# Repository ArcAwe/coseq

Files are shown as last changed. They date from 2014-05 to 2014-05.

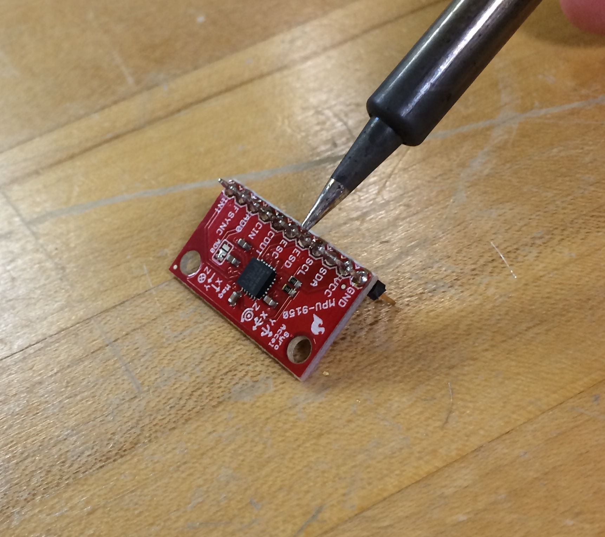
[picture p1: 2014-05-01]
photos/IMG_0470.jpg

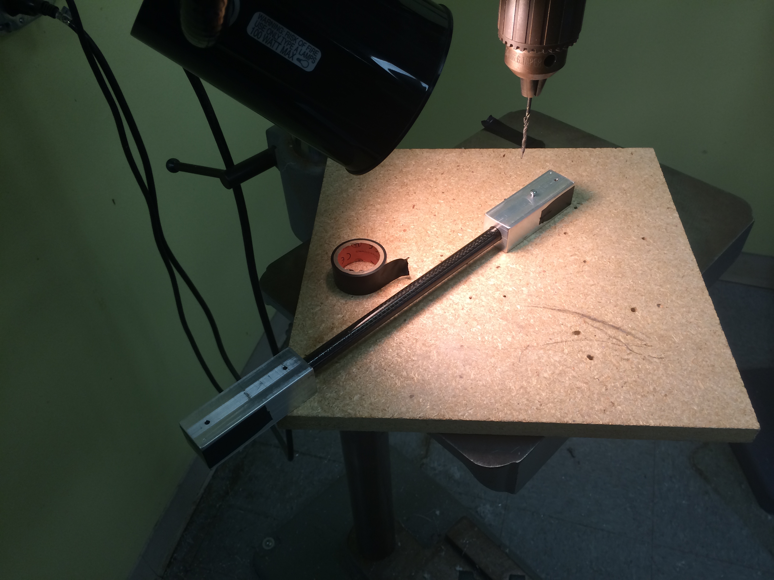
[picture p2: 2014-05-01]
photos/IMG_0632.JPG

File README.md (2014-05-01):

<i>coseq</i>
============

Cadet Open Source Extensible Quadcopter (COSEQ) Design Documents and Code.

Written and compiled by G. Holland Gibson - 2014
Originally as part of his Honors Project @ The United States Military Academy. 

Open Source
===========

This is a primarily open-source design (and work in progress) to accomplish 3 extensible and adaptable components that operate 
independently of each other in order to provide a stable airborne platform in a quadcopter form.

Written under the MIT license except where otherwise noted (using other peoples' open source code). See LICENSE for more info.

1] Hardware:
-----------
The Hardware is a very stable, and strong, yet lightweight construction

2] Controller: 
-------------
The controller uses Python running on a raspberry pi (battery powered) with a USB controller/gamepad.

3] Embedded Electronics: 
-----------------------
Parallax Propeller as host system.

Open Source / Freeware used:
============================
Google SketchUp
    http://www.sketchup.com/<br>
SimpleIDE
    http://learn.parallax.com/propeller-c-set-simpleide<br>
TextWrangler
    http://www.barebones.com/products/textwrangler/<br>
netfabb Basic
    http://www.netfabb.com/basic.php<br>

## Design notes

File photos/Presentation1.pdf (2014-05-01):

# Cadet Open Source Extensible Quadcopter

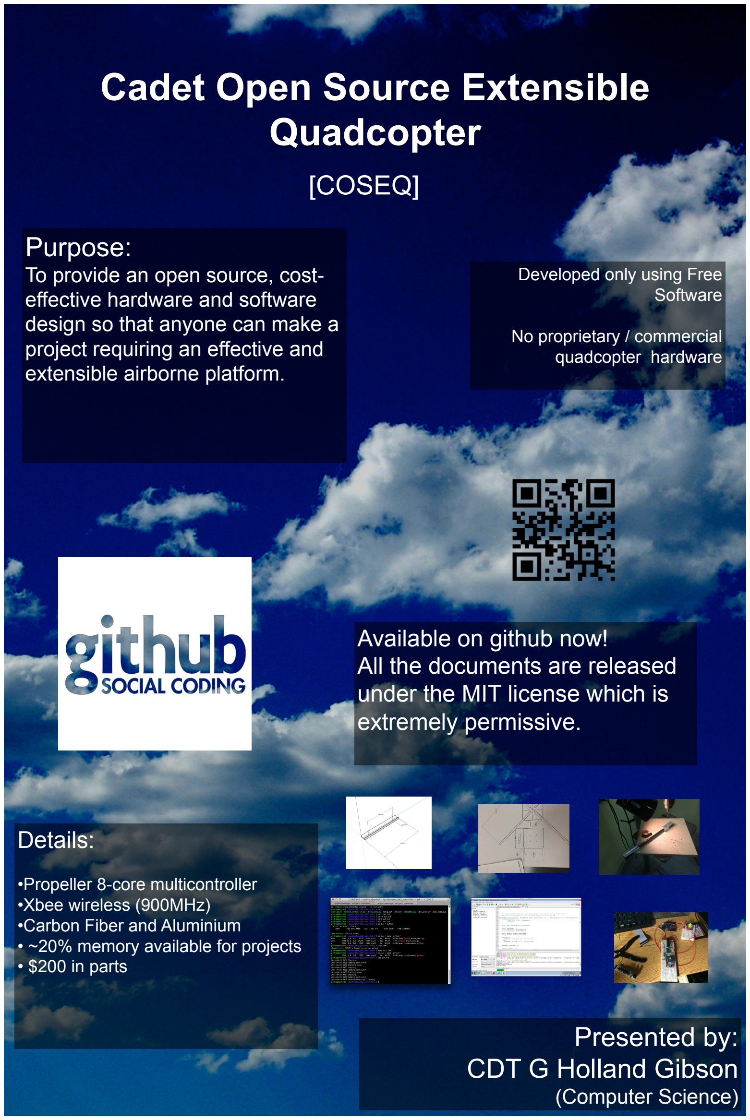
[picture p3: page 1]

## [COSEQ]

## Presented by: CDT G Holland Gibson

(Computer Science)

## Purpose:

To provide an open source, costeffective hardware and software design so that anyone can make a project requiring an effective and extensible airborne platform.

## Available on github now! All the documents are released under the MIT license which is

extremely permissive.

Developed only using Free
Software

No proprietary / commercial quadcopter hardware

## Details:

•Propeller 8-core multicontroller •Xbee wireless (900MHz)
•Carbon Fiber and Aluminium
- ~20% memory available for projects
- $200 in parts

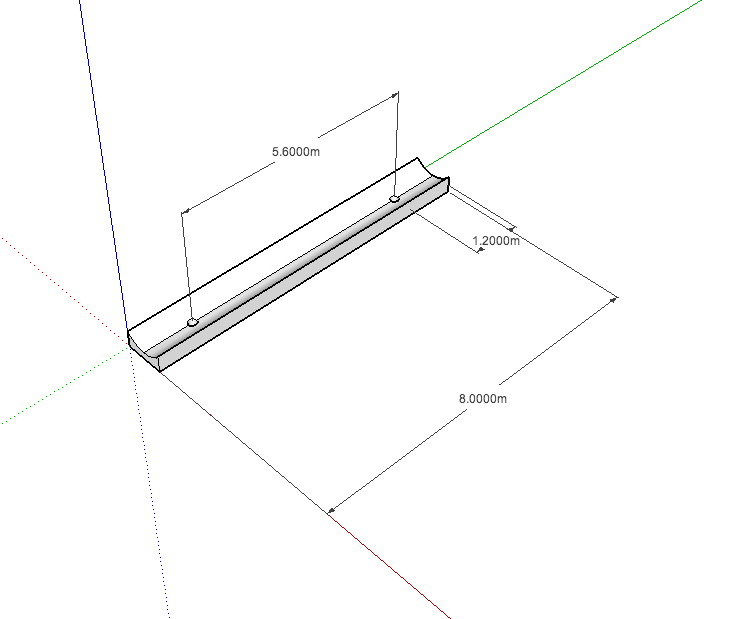
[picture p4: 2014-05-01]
photos/Foot Schematic.png

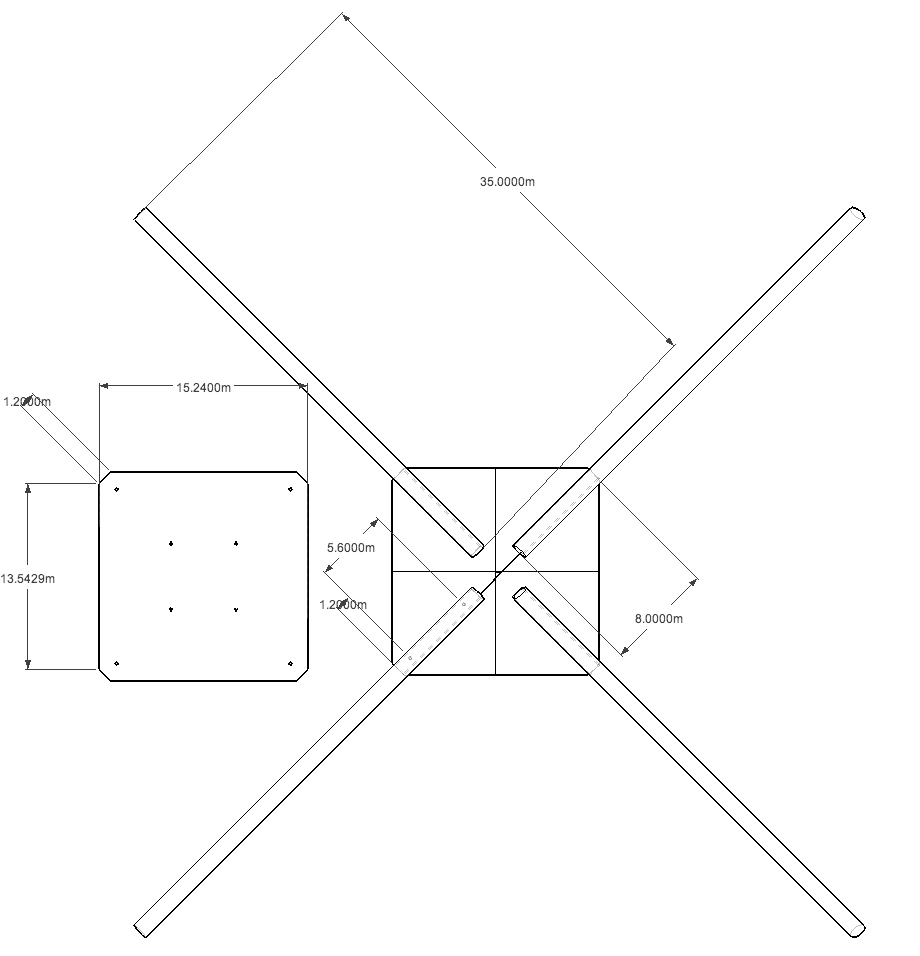
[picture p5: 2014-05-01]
Hardware/Overall Dimensions.png

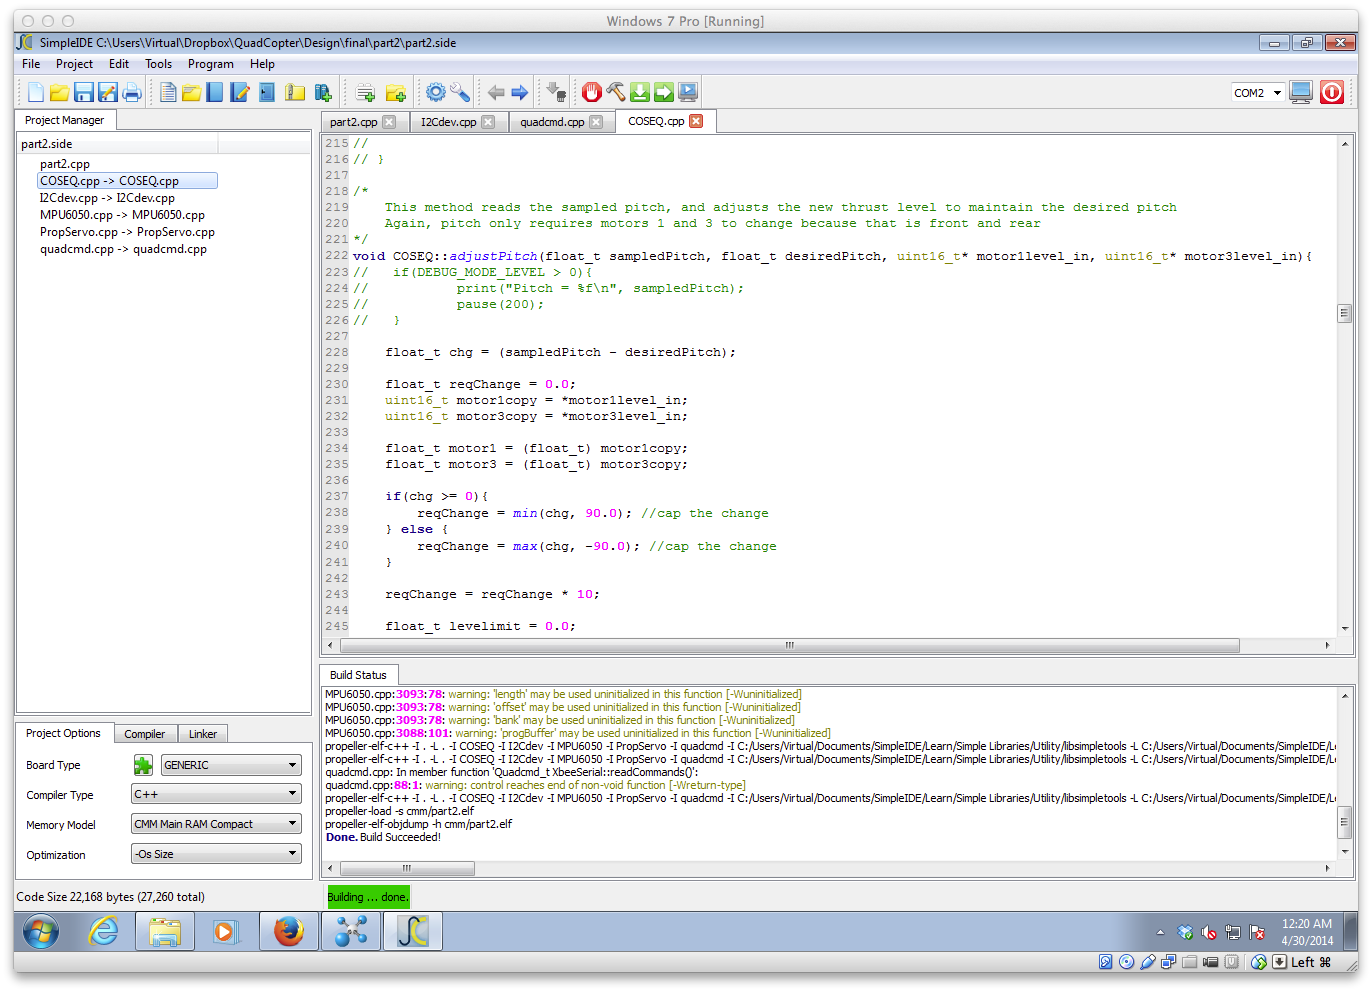
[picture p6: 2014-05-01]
photos/Screenshot.png

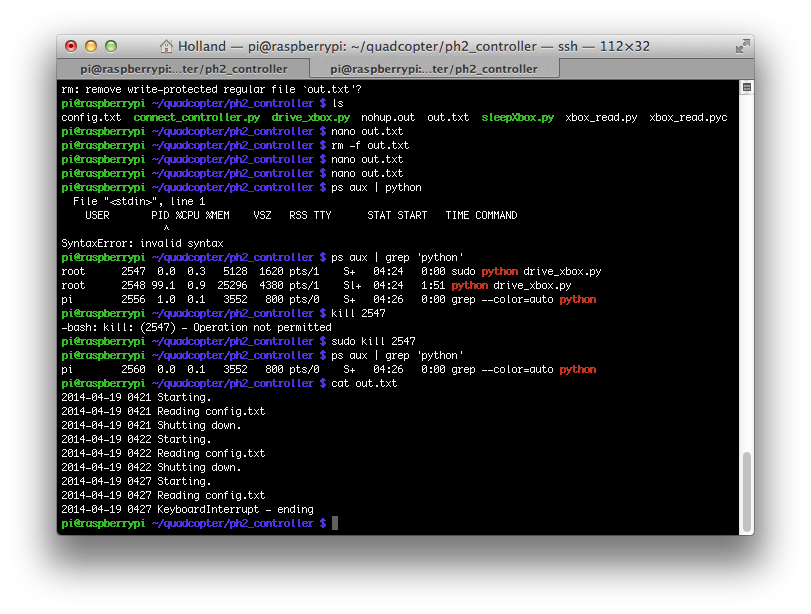
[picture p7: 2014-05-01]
photos/Screen Shot 2014-04-30 at 00.21.10 .png

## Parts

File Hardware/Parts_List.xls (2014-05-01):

COSEQ PARTS LIST | NAME: | QNTY | UNIT PRICE | TOTAL PRICE
ELECTRONICS
ESC | TURNIGY Plush 30amp Speed Controller (http://www.hobbyking.com/hobbyking/store/uh_viewItem.asp?idProduct=2164) | 4 | $13.13 | $52.52
Battery | Turnigy 5000mAh 3S 25C Lipo Pack (http://www.hobbyking.com/hobbyking/store/uh_viewItem.asp?idProduct=9183) | 1 | $29.97 | $29.97 | These 3 items must be researched and bought as a package
Motor | Turnigy 2217 20turn 860kv 22A Outrunner (http://www.hobbyking.com/hobbyking/store/uh_viewItem.asp?idProduct=5691) | 4 | $15.58 | $62.32
Charger | Turnigy Accucel-6 50W 6A Balancer/Charger w/ Accessories (http://www.hobbyking.com/hobbyking/store/uh_viewItem.asp?idProduct=7028) | 1 | $22.95 | $22.95
Controller | Parallax Propeller ASC+ (http://www.parallax.com/product/32214) | 1 | $49.99 | $49.99 | I chose the Arduino form factor for convienience, the quickstart ($35) should be fine
 | Xbee Breakout Board (https://www.sparkfun.com/products/8276) | 1 | $2.95 | $2.95
 | Bare Arduino PCB (https://www.sparkfun.com/products/11665) | 1 | $4.95 | $4.95
IMU | MPU9150 + breakout board (https://www.sparkfun.com/products/11486) | 1 | $39.95 | $39.95 | The MPU6050 will also work with only ver minor configuration changes to the code
Wireless Xbee | XBee Pro 900 RPSMA (https://www.sparkfun.com/products/9099) | 2 | $37.95 | $75.90 | Any Xbee will work - the 900MHz band is very long range however
 |  |  |  | $0.00
ELECTRICAL HARDWARE |  |  |  | $0.00
 | HXT 4mm to 4 X 3.5mm bullet Multistar ESC Power Breakout Cable (http://www.hobbyking.com/hobbyking/store/uh_viewItem.asp?idProduct=25483) | 1 | $3.19 | $3.19
 | 900Mhz Duck Antenna RP-SMA (https://www.sparkfun.com/products/9143) | 2 | $7.95 | $15.90
 | Wire, 16AWG | 1 | $5.70 | $5.70 | Any 16AWG wire will suffice, you only need a few feet
 | 40x3.5mm Bullet Banana Plugs (http://www.amazon.com/dp/B00DGL1T1O/ref=pe_385040_30332200_pe_309540_26725410_item) | 1 | $6.30 | $6.30
 | 10x4.5 SF Props Black CW (2pc) CCW (2pc) (http://www.hobbyking.com/hobbyking/store/uh_viewItem.asp?idProduct=25824) | 2 | $3.15 | $6.30 | Extras are nice!
LOAD BEARING HARDWARE
Arms | HK450 carbon tail boom (http://www.hobbyking.com/hobbyking/store/uh_viewItem.asp?idProduct=17126) | 4 | $2.85 | $11.40
 | #13 Rubber O-ring (package of 10) | 1 | $2.37 | $2.37 | For attaching the props to the prop-savers
 | 7075-T6 ALUMINUM SHEET, 0.040" THICK, 6.0x6.0" SQUARE (https://www.onlinemetals.com/merchant.cfm?pid=10611&step=4) | 3 | $3.96 | $11.88 | The 3rd was to have an extra, this is a great balance of strength and weight. I don't recommend moving away from this one
 | Fiberglass Motor Mount, generic, package of 4 (http://www.ebay.com/sch/i.html?_nkw=fiber+motor+mount&_sacat=0&_from=R40) | 1 | $4.99 | $4.99
 | Screws, Nuts, washers… |  |  | $0.00
 | Tupperware lid to protect electronics |  |  | $0.00
 | Electrical Tape |  |  | $0.00
 | Hook & Loop (Velcro) Tape |  |  | $0.00
 |  |  | TOTAL | $409.53

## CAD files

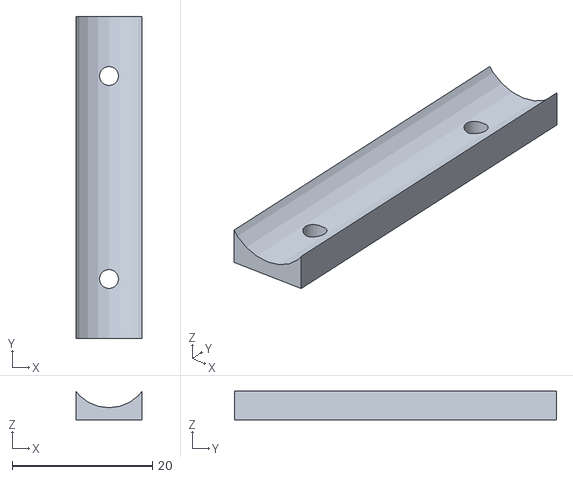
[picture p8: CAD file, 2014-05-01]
Hardware/STL/motor_foot_scaled.stl
9.44 x 46.0 x 4.12

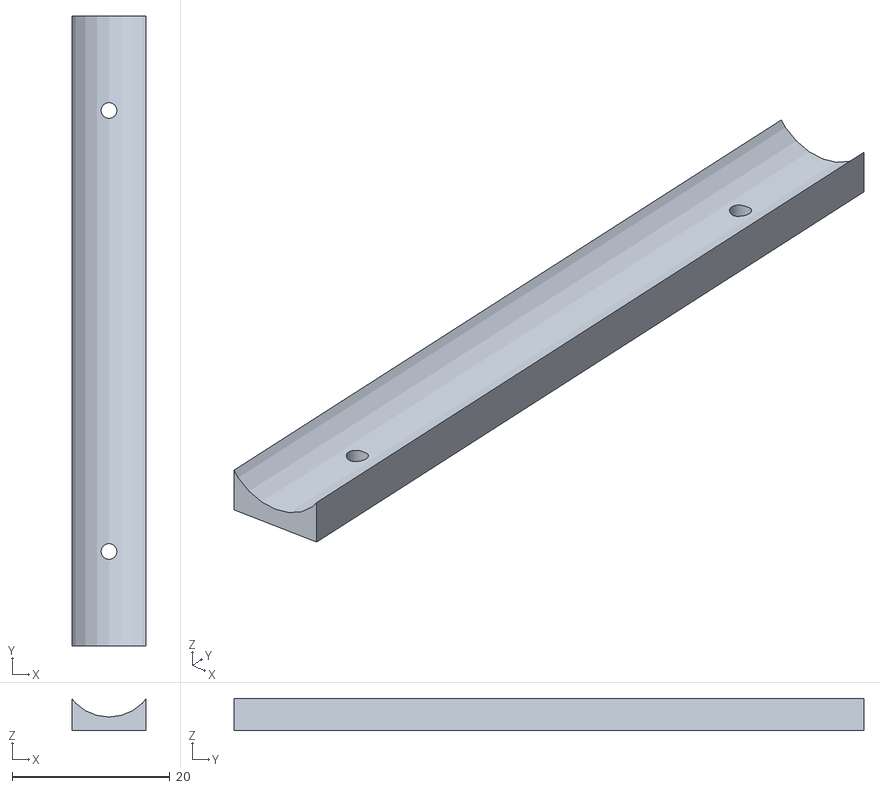
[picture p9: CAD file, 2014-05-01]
Hardware/STL/foot2scaled.stl
9.44 x 80.0 x 4.12

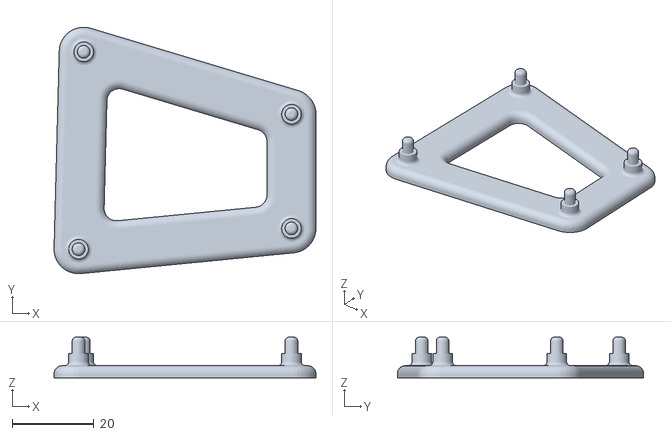
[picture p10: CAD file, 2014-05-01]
Hardware/STL/Arduino_Holder.STL
64.1 x 60.3 x 10.0

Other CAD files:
Hardware/SketchUp/foot.skp
Hardware/SketchUp/gopromount.skp
Hardware/SketchUp/motor_foot.skp
Hardware/SketchUp/overalldesign view 2.skp
Hardware/SketchUp/overalldesign.skp
Hardware/SketchUp/view1.skp

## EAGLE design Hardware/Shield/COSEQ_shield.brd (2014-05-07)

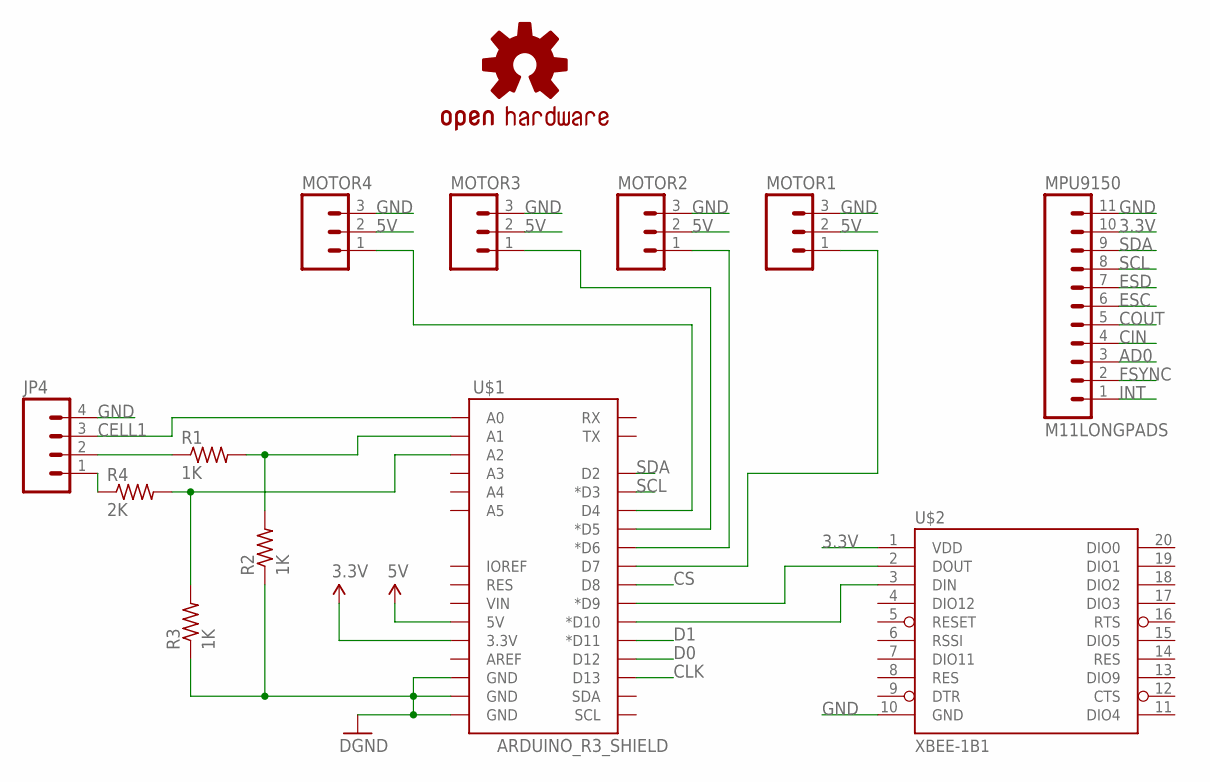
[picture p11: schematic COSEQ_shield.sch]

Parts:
JP4: M04LONGPADS; 1X04_LONGPADS
LOGO1: OSHW-LOGOL; OSHW-LOGO-L
MOTOR1, MOTOR2, MOTOR3, MOTOR4: M03LONGPADS; 1X03_LONGPADS
MPU9150: M11LONGPADS; 1X11_LONGPADS
R1, R2, R3: 1K; RESISTOR
R4: 2K; RESISTOR
U$1: ARDUINO_R3_SHIELD; UNO_R3_SHIELD
U$2: XBEE-1B1; XBEE-1

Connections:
3.3V: MPU9150.10, U$1.3.3V, U$2.1 (VDD)
5V: MOTOR1.2, MOTOR2.2, MOTOR3.2, MOTOR4.2, U$1.5V
AD0: MPU9150.3
CELL1: JP4.3, U$1.A0
CIN: MPU9150.4
CLK: U$1.D13
COUT: MPU9150.5
CS: U$1.D8
D0: U$1.D12
D1: U$1.D11 (*D11)
ESC: MPU9150.6
ESD: MPU9150.7
FSYNC: MPU9150.2
GND: JP4.4, MOTOR1.3, MOTOR2.3, MOTOR3.3, MOTOR4.3, MPU9150.11, R2.1, R3.1, U$1.GND@0 (GND), U$1.GND@1 (GND), U$1.GND@2 (GND), U$2.10 (GND)
INT: MPU9150.1
M1: MOTOR4.1, U$1.D4
M2: MOTOR3.1, U$1.D5 (*D5)
M3: MOTOR2.1, U$1.D6 (*D6)
M4: MOTOR1.1, U$1.D7
unnamed: JP4.2, R1.1
unnamed: U$1.D10 (*D10), U$2.3 (DIN)
unnamed: R1.2, R2.2, U$1.A1
unnamed: U$1.D9 (*D9), U$2.2 (DOUT)
unnamed: JP4.1, R4.1
unnamed: R3.2, R4.2, U$1.A2
SCL: MPU9150.8, U$1.D3 (*D3)
SDA: MPU9150.9, U$1.D2

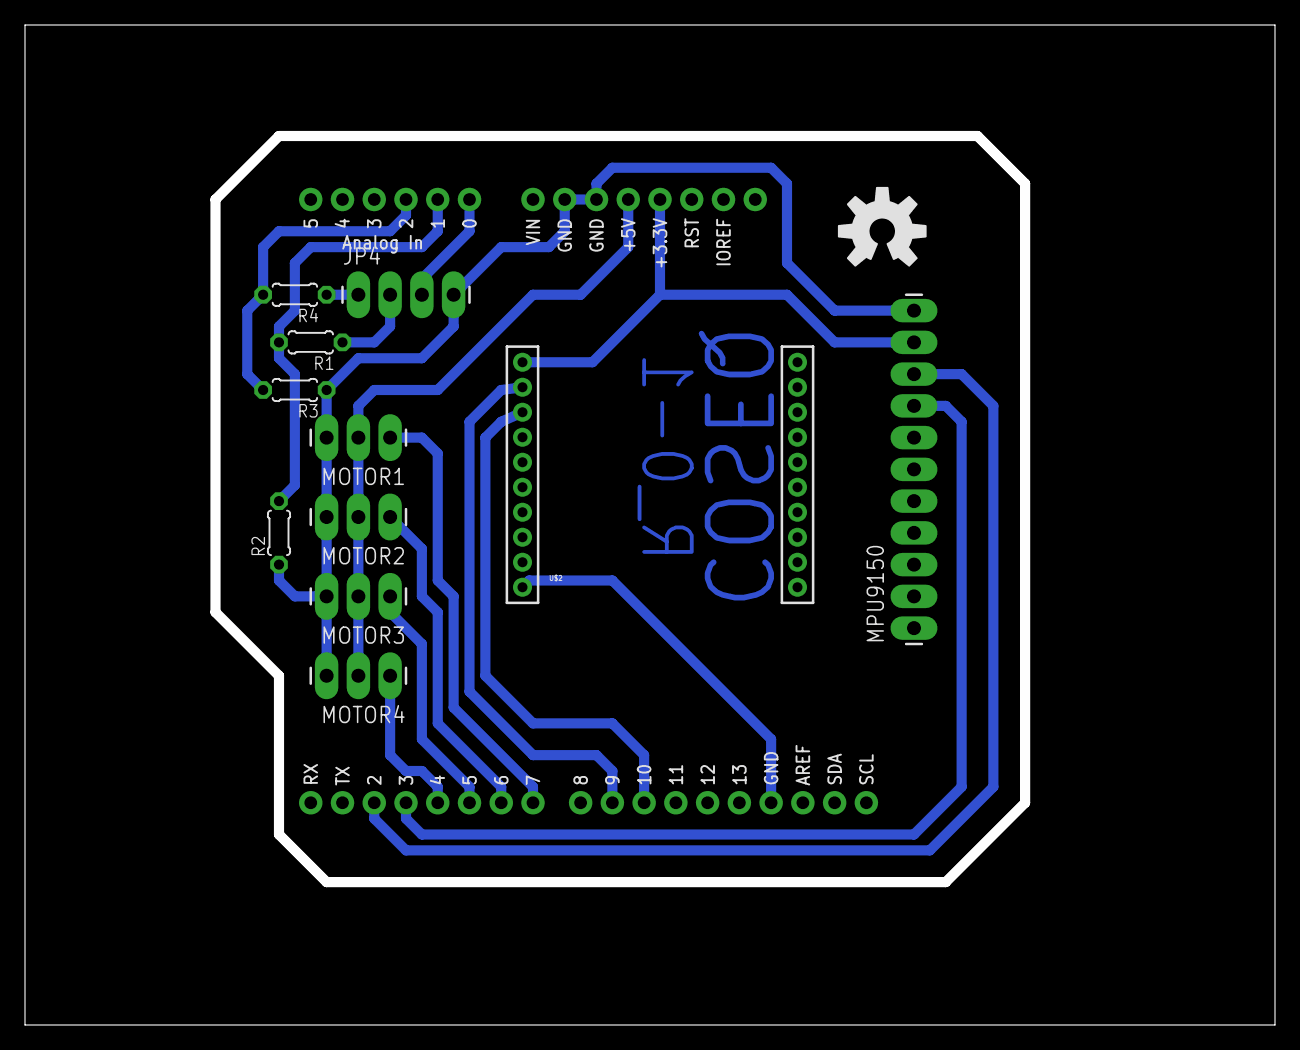
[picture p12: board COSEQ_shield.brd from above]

Board: 2 copper layers, 100.0 x 80.0 mm, 13 parts (0 on the bottom side), 16 nets.

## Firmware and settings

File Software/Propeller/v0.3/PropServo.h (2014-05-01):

#ifndef _COSEQ_PROP_CONTROL_H_
#define _COSEQ_PROP_CONTROL_H_

#include "simpletools.h"
#include "servo.h"

#define DEFAULT_1_PIN 9
#define DEFAULT_2_PIN 8
#define DEFAULT_3_PIN 7
#define DEFAULT_4_PIN 6

#define stoprpm 700
#define minrpm 770
#define maxrpm 2000

#define MOTOR_FRONT 0
#define MOTOR_RIGHT 1
#define MOTOR_REAR 2
#define MOTOR_LEFT 3

class PropServo {
  public:
    PropServo();
    PropServo(uint8_t motor1pin, uint8_t motor2pin, uint8_t motor3pin, uint8_t motor4pin);
    
    //This is used to determine when the class is done initializing the ESCs
    //It becomes 1 once that is complete (so the calls of setThrust / updateServoRPM
    //will only occur from another class - to help with concurrency issues)
    //this takes at least 6 seconds
    static uint8_t PropServoStatus;
    
    static void setThrust(uint8_t motor, uint16_t thrust);
    static void updateServoRPM();
    
  private:
    static uint8_t prop1pin;
    static uint8_t prop2pin;
    static uint8_t prop3pin;
    static uint8_t prop4pin;
    static double_t delta;
    static uint16_t rpm[4];
    
    void calibrate();
};
#endif /* _COSEQ_PROP_CONTROL_H_ */

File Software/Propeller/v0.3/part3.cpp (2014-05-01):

/**

Main Code to run the COSEQ System.

Holland Gibson
May 2014

(USMA '14 Honors Project)

See readme for more information.
**/
#include "COSEQ.h"
#include "simpletools.h"
#include "servo.h"
#include "fdserial.h"
#include "Quadcmd.h"
#include "PropServo.h"


/**
 * This is the main program file.
 */
int main(void)
{
  //should help cogs print to terminal
    extern text_t *dport_ptr; // default debug port pointer gets reassigned to fdserial.
    simpleterm_close();
    dport_ptr = (fdserial_open(31,30,0,115200));

    uint8_t debug_mode = 0;
  
    COSEQ system = COSEQ();
    print("Starting COSEQ.\n");
    system.start(); 
  
    //all the threads are running on cogs, so we relax
    while(true){
        //sanity check with debug
        
        //this is on a pause 1000ms so it shouldn't interfere with anything (although it might)
        if(debug_mode == 1){
            Quadcmd_t cmd = COSEQ::xbcmd;
    
            print("CMD: %u\t", cmd.CMD_TYPE);
            print("%u\t", cmd.data_bytes[0]);
            print("%u\t", cmd.data_bytes[1]);
            print("%u\t", cmd.data_bytes[2]);
            print("%u\t", cmd.data_bytes[3]);
            print("%u\t", cmd.data_bytes[4]);
            print("%u",   cmd.data_bytes[5]);
            print("\n");
            
        } else if(debug_mode == 2) {
            print("%u\t", COSEQ::motor1debug);
            print("%u\t", COSEQ::motor2debug);
            print("%u\t", COSEQ::motor3debug);
            print("%u",   COSEQ::motor4debug);
            print("\n");
            
        } else if(debug_mode == 3) {
            while(COSEQ::mpu9150Lock == 1){
                //block
            }
            float p = COSEQ::spitch;
            float r = COSEQ::sroll;
            print("%f\t", p);
            print("%f\t", r);
            print("\n");
        }
        pause(1000);
    }
  //system.listEEPROM();
}

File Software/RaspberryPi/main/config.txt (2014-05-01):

# This is the congif file, right now it only accepts CMD_TYPE
# CMD_TYPE:
# 0 = NOT USED
# 1 = complete manual (this is very difficult to fly with, but good for testing)
# 2 = manual thrust, autolevel to angle given by controller
CMD_TYPE=2

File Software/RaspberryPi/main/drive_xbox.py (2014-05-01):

#! usr/bin/python

import time
import serial
from threading import *
from array import *
import xbox_read
import sys
import datetime

thrust = float(0.0)
pitch = float(0.0)
roll = float(0.0)
yaw = float(0.0)

CMD_TYPE = 0

outf = open("/home/pi/quadcopter/main/out.txt","a")

# serialEvent = Event()
# serialCondition = Condition()
# dataLock = Lock()
# serialSem = BoundedSemaphore()
# dataSem = BoundedSemaphore()

handshake = 1


#commandString = array('B');
commandString = [0,0,0]


def new_value(current, pos): # Function for changing range
     if pos == "left-up":
                     return (((current - 0) * (180 - 90)) / (100 - 0)) + 90 # Change range from 0 - 100 to 90 - 180
     elif pos == "right-down":
            return (((current - 0) * (0 - 90)) / (100 - 0)) + 90 # Change range from 0 - 100 to 90 - 0


def right_joystick():
    global thrust, pitch, roll, yaw, handshake, commandString
    for event in xbox_read.event_stream(deadzone=2000, scale=255):
        if event.key == 'RT' or event.key == 'LT':
            thrust = event.value
        elif event.key == 'X1': #left stick
            yaw = event.value
        elif event.key == 'X2':
            roll = event.value
        elif event.key == 'Y2':
            pitch = event.value
        
        if(handshake == 1):
            commandString = formatCommand(CMD_TYPE) #if we can we combine them to send off
        

# Format the byte string
def formatCommand(format):
    global thrust, pitch, roll, yaw, handshake, commandString
    command = []

    #see quadcmd.h for API / standards

    if format == 1: #full manual
        #positive pitch = pitch down

        #positive roll = roll right
        
        motor1 = float()
        motor2 = float()
        motor3 = float()
        motor4 = float()
        
        #  /4 to soften control
        motor1 = (-pitch/4.0)+255.0
        motor3 = (pitch/4.0)+255.0
        motor2 = (-roll/4.0)+255.0
        motor4 = (roll/4.0)+255.0
        
        motor1 *= (thrust/255.0)
        motor2 *= (thrust/255.0)
        motor3 *= (thrust/255.0)
        motor4 *= (thrust/255.0)
        
        yaw /= 2
        
        if(yaw <= 0):
            yaw = max(yaw, -254)
            #turn left - bring down 2 and 4
            yawFactor = (255.0+yaw)/255.0
            motor2 *= yawFactor
            motor4 *= yawFactor
            motor1 /= yawFactor
            motor3 /= yawFactor
        else: #if(yaw > 0):
            yaw = min(yaw, 254)
            #turn right - bring down 1 and 3
            yawFactor = (255.0-yaw)/255.0
            motor1 *= yawFactor
            motor3 *= yawFactor
            motor2 /= yawFactor
            motor4 /= yawFactor
        # do nothing if abs(yaw) = 255 (DIV BY 0 ERROR)
        
        
        motor1final = int(min(motor1, 255))
        motor2final = int(min(motor2, 255))
        motor3final = int(min(motor3, 255))
        motor4final = int(min(motor4, 255))
        
#         motor1final = min(motor1, 255)
#         motor2final = min(motor1, 255)
#         motor3final = min(motor1, 255)
#         motor4final = min(motor1, 255)

        checksum = (1+motor1final+motor2final+motor3final+motor4final) & 0xff
        
        command.append(1)
        command.append(motor1final)
        command.append(motor2final) #only between 0-254 so we good
        command.append(motor3final)
        command.append(motor4final)
        command.append(0) #unused
        command.append(0) #unused
        command.append(checksum) #checksum?
        
#         print command
    elif (format == 2):
        thrustFinal = int(thrust)
        
        pitchVector = float()
        rollVector = float()
        yawVector = float()
        
        #pitch *= -1
        #roll *= -1
        
        pitchVector = max((-pitch/3.0)/2.0 + 127, 0)
        rollVector = max((-roll/3.0)/2.0 + 127, 0)
        yawVector = (yaw/8.0 + 255.0)/2.0
        
        pitchFinal = int(pitchVector)
        rollFinal = int(rollVector)
        yawFinal = int(yawVector)
        
        checksum = int()
        checksum = int(2+thrust+pitchFinal+rollFinal+yawFinal) & 0xff
        
        command.append(2)
        command.append(thrustFinal)
        command.append(pitchFinal)
        command.append(rollFinal)
        command.append(yawFinal)
        command.append(0)
        command.append(0)
        command.append(checksum)
        
    return command

def send_command():
    global thrust, pitch, roll, yaw
    try:
        serialPort = serial.Serial("/dev/ttyAMA0", 115200, timeout=0)
        serialPort.open()
        
        print "Sending commands.."
        
        while(True):
            handshake = 0 #stop the commandString from being updated
            cmdCopy = array('B',commandString)
            
            if(commandString[0] > 0):
                d = serialPort.write(cmdCopy)
#                 time.sleep(0.5)
#                 r = 'A'
#                 while(r != ''):
#                     r = serialPort.read(1)
#                     sys.stdout.write(r);
#                 print "\\"
                #serialPort.flushInput()
                #print str(pitch) + "\t" + str(roll) + "\t" + str(yaw)
                print cmdCopy
                #print_out(cmdCopy)

            handshake = 1 #let it keep getting updated
            time.sleep(0.02) #0.2 and up should work
    finally:
        serialPort.close()
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

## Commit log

2014-05-01 Added Hardware Directory
    [Arduino_Holder.STL, Parts_List.xls, foot.skp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]
2014-05-01 Propeller Software
2014-05-01 Raspberry Pi Software
    [config.txt]
2014-05-07 Added Eagle files for the ASC+ shield
    [COSEQ_shield.brd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]

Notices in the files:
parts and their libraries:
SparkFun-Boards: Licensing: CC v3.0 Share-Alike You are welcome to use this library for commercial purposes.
